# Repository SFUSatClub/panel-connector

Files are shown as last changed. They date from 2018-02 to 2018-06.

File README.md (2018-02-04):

# panel-connector
KiCad project of the connector board connecting the 4 outer panels to the internal PC104 stackup.

This repository uses the SFU Satellite Team's KiCad component library as a submodule.
To start working on the repository:

```
1. Open the git shell
2. Navigate to the directory you wish to place the repository inside
3. git clone --recursive "https://github.com/SFUSatClub/panel-connector.git"
4. cd .\panel-connector\KiCad-Lib\
5. git checkout master
```

If you modify either the component schematic or footprint libraries you must push those changes to the SFUSatClub/KiCad-Lib repository.

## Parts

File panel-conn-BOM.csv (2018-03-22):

reference | name | Digikey PN | number
R224,R3,R201,R211,R221,R231,R101,R111,R121 R223,R232,R233,R212,R215,R204,R205,R4,R131,R2*1,R1*1 | 0R | 311-0.0LBCT-ND | 21
J7 | B3B-XH-A(LF)(SN) | 455-2248-ND | 1
J7 | B3B-XH-A(LF)(SN) mating | 455-2219-ND | 1
J105,J2*0 | MOLEX_FFC-14 | WM1442CT-ND | 6
U2*0 | ADG728 | ADG728BRUZ-ND | 4
U1*0 | SPV1040 | 497-11417-ND | 8
L1*0 | L_10u0_10%_1.42A_2-SMD, | 495-5656-1-ND | 8
R1*5 | 1M0 | RG20P1.0MBCT-ND | 8
D1*0 | SMM4F5.0A-TR | 497-15660-1-ND | 8
C1*5 | 4u7F | 587-1302-1-ND | 8
C1*4,C1*0 | 10uF | 445-7658-1-ND | 16
R1*4 | 10m0 | WSLP-.01CT-ND | 8
R1*2, R1*3, R1*0 | 1k0 | RG20P1.0KBCT-ND | 24
C1*3, C1*2 | 1u0F | 445-1358-1-ND | 16
C1*1 | 100nF | 445-14401-1-ND | 8
R1*6 | 357k | P357KDACT-ND | 8

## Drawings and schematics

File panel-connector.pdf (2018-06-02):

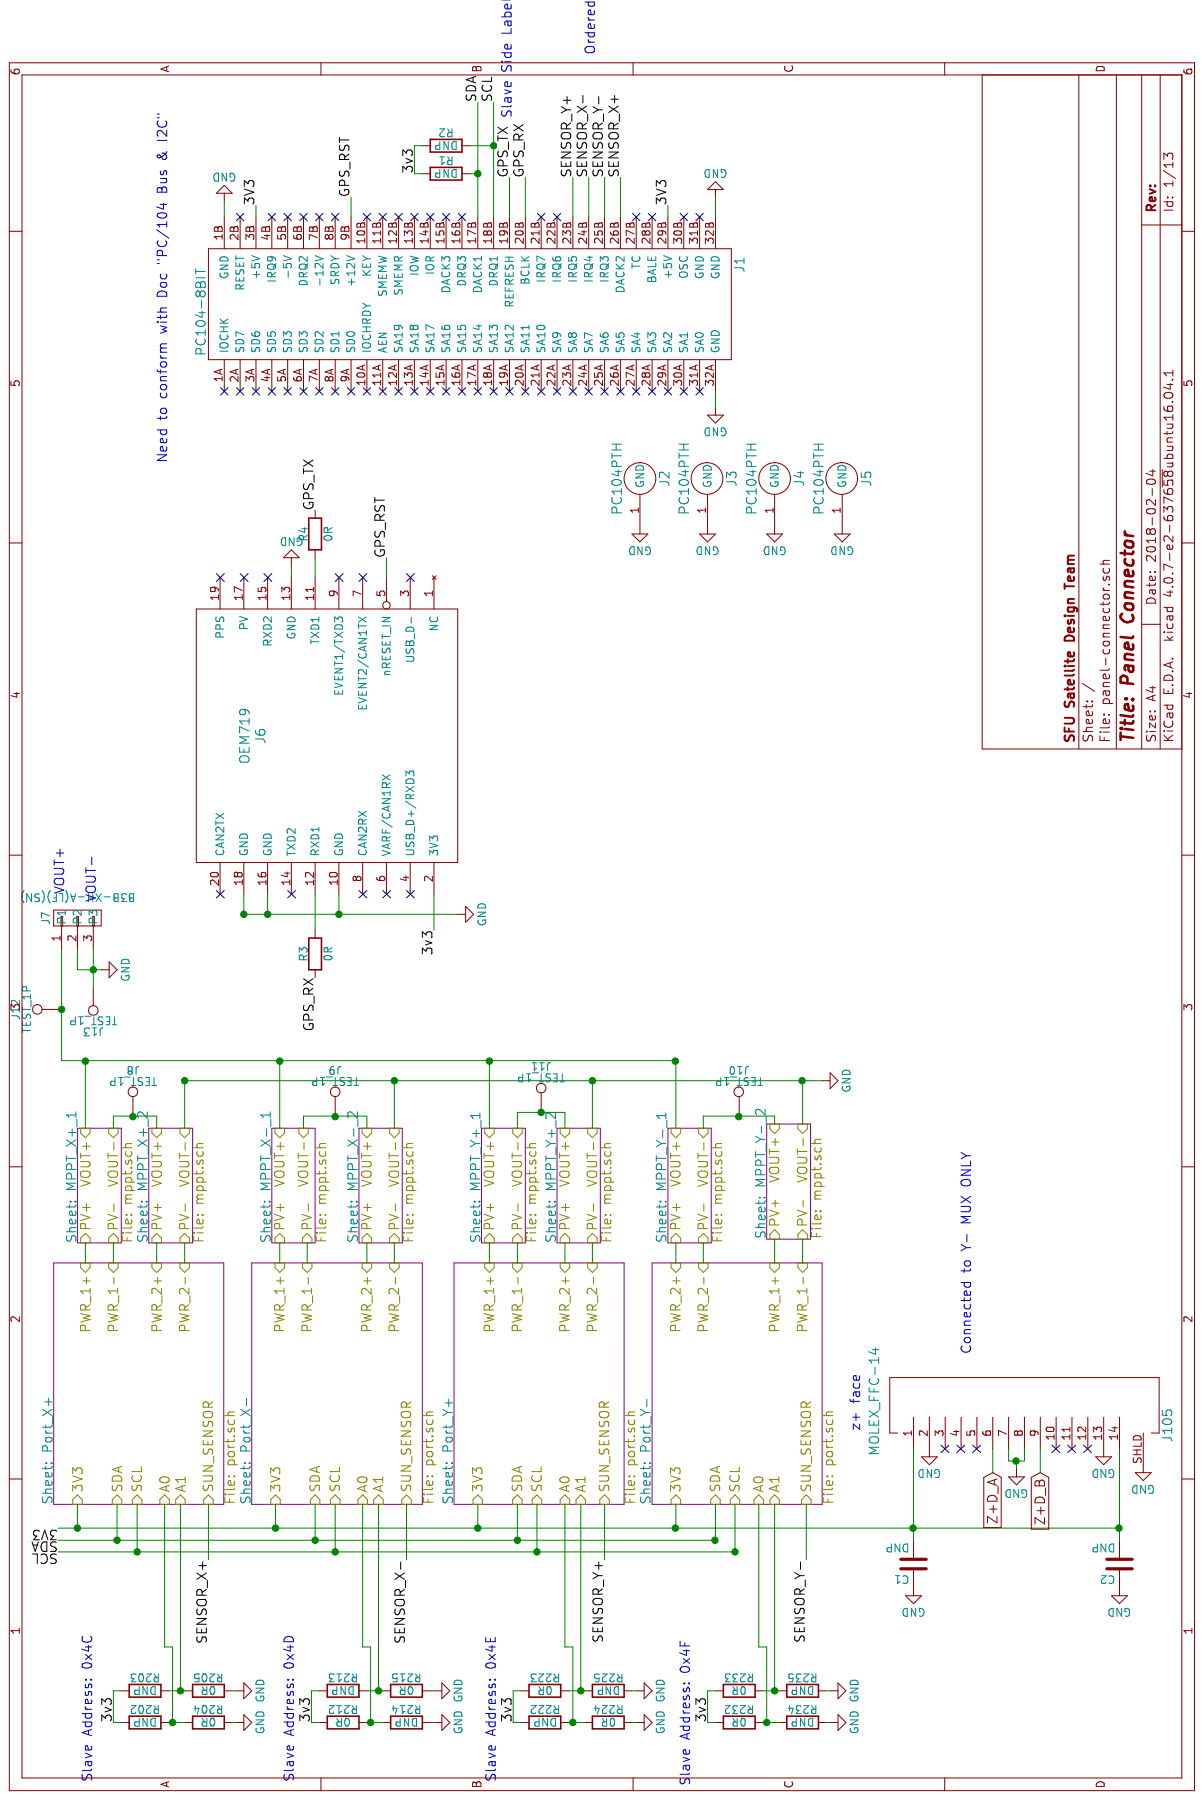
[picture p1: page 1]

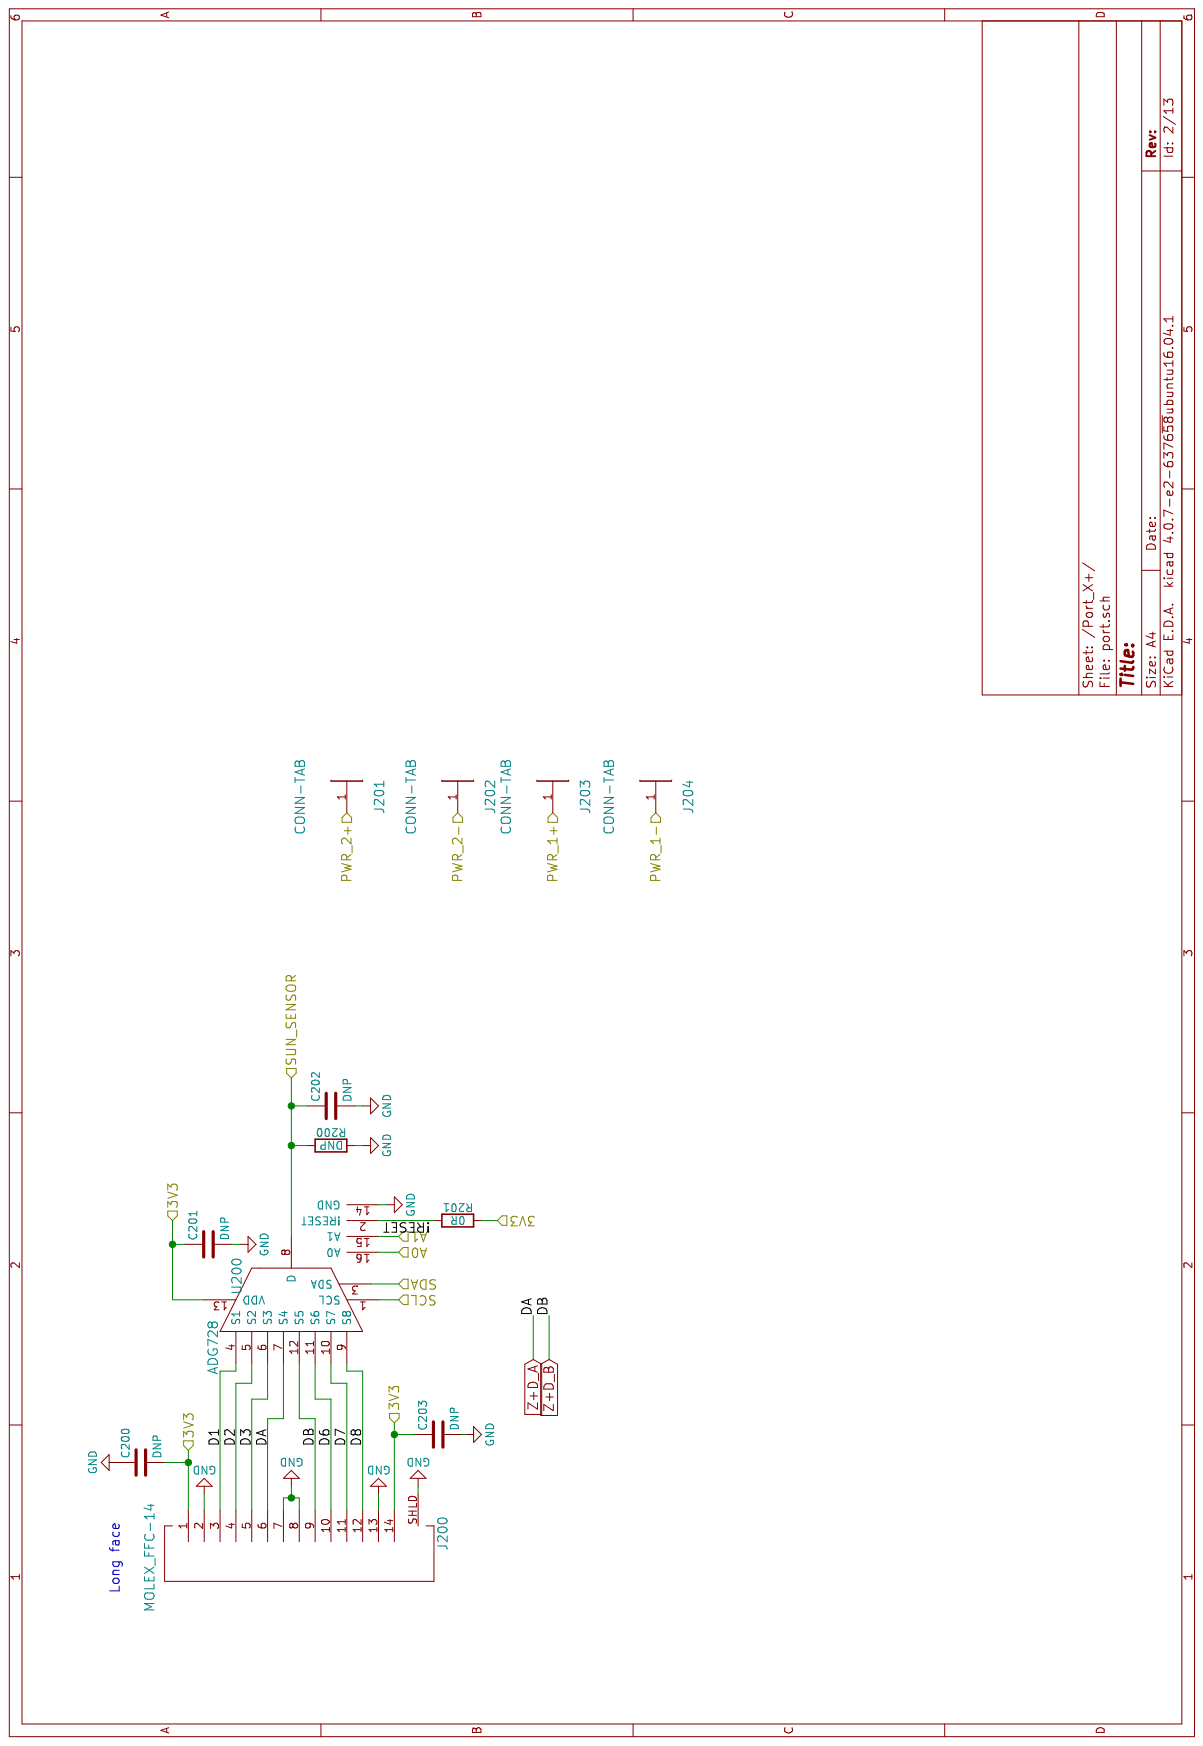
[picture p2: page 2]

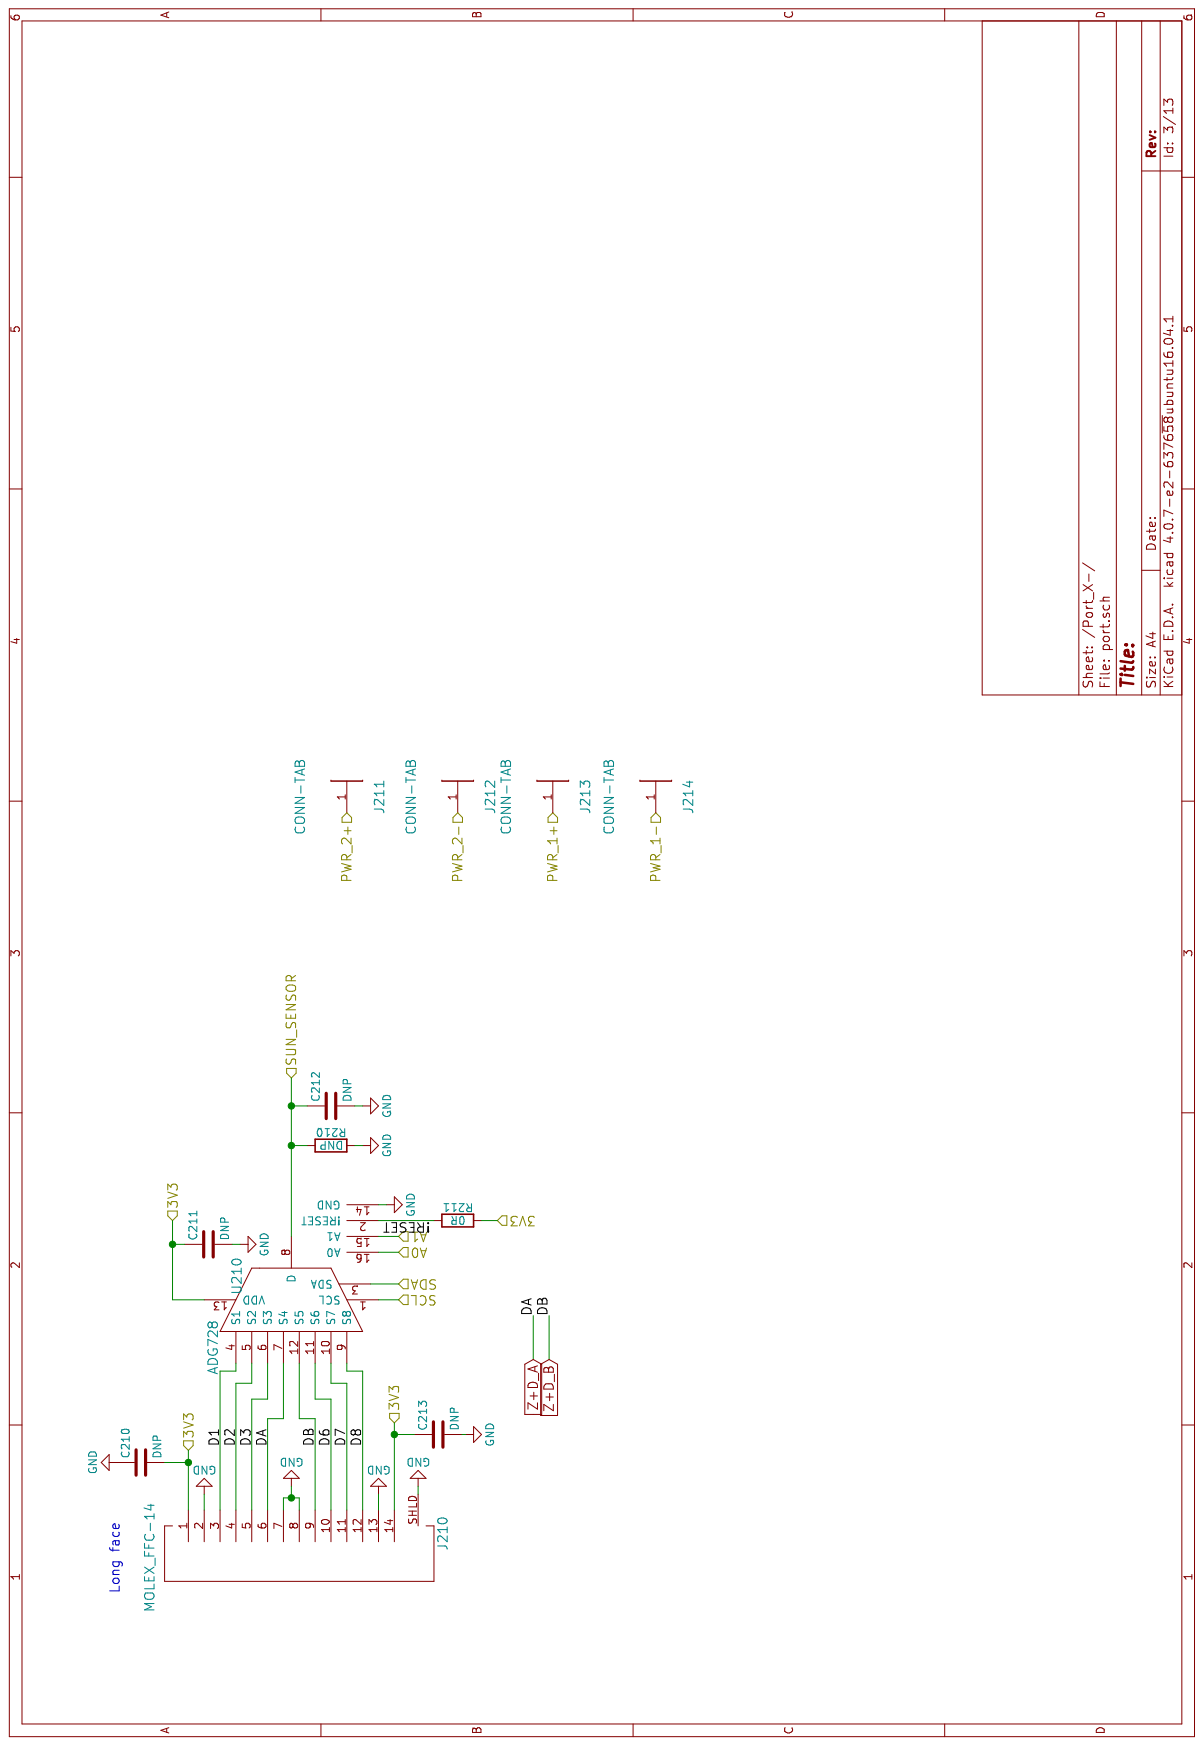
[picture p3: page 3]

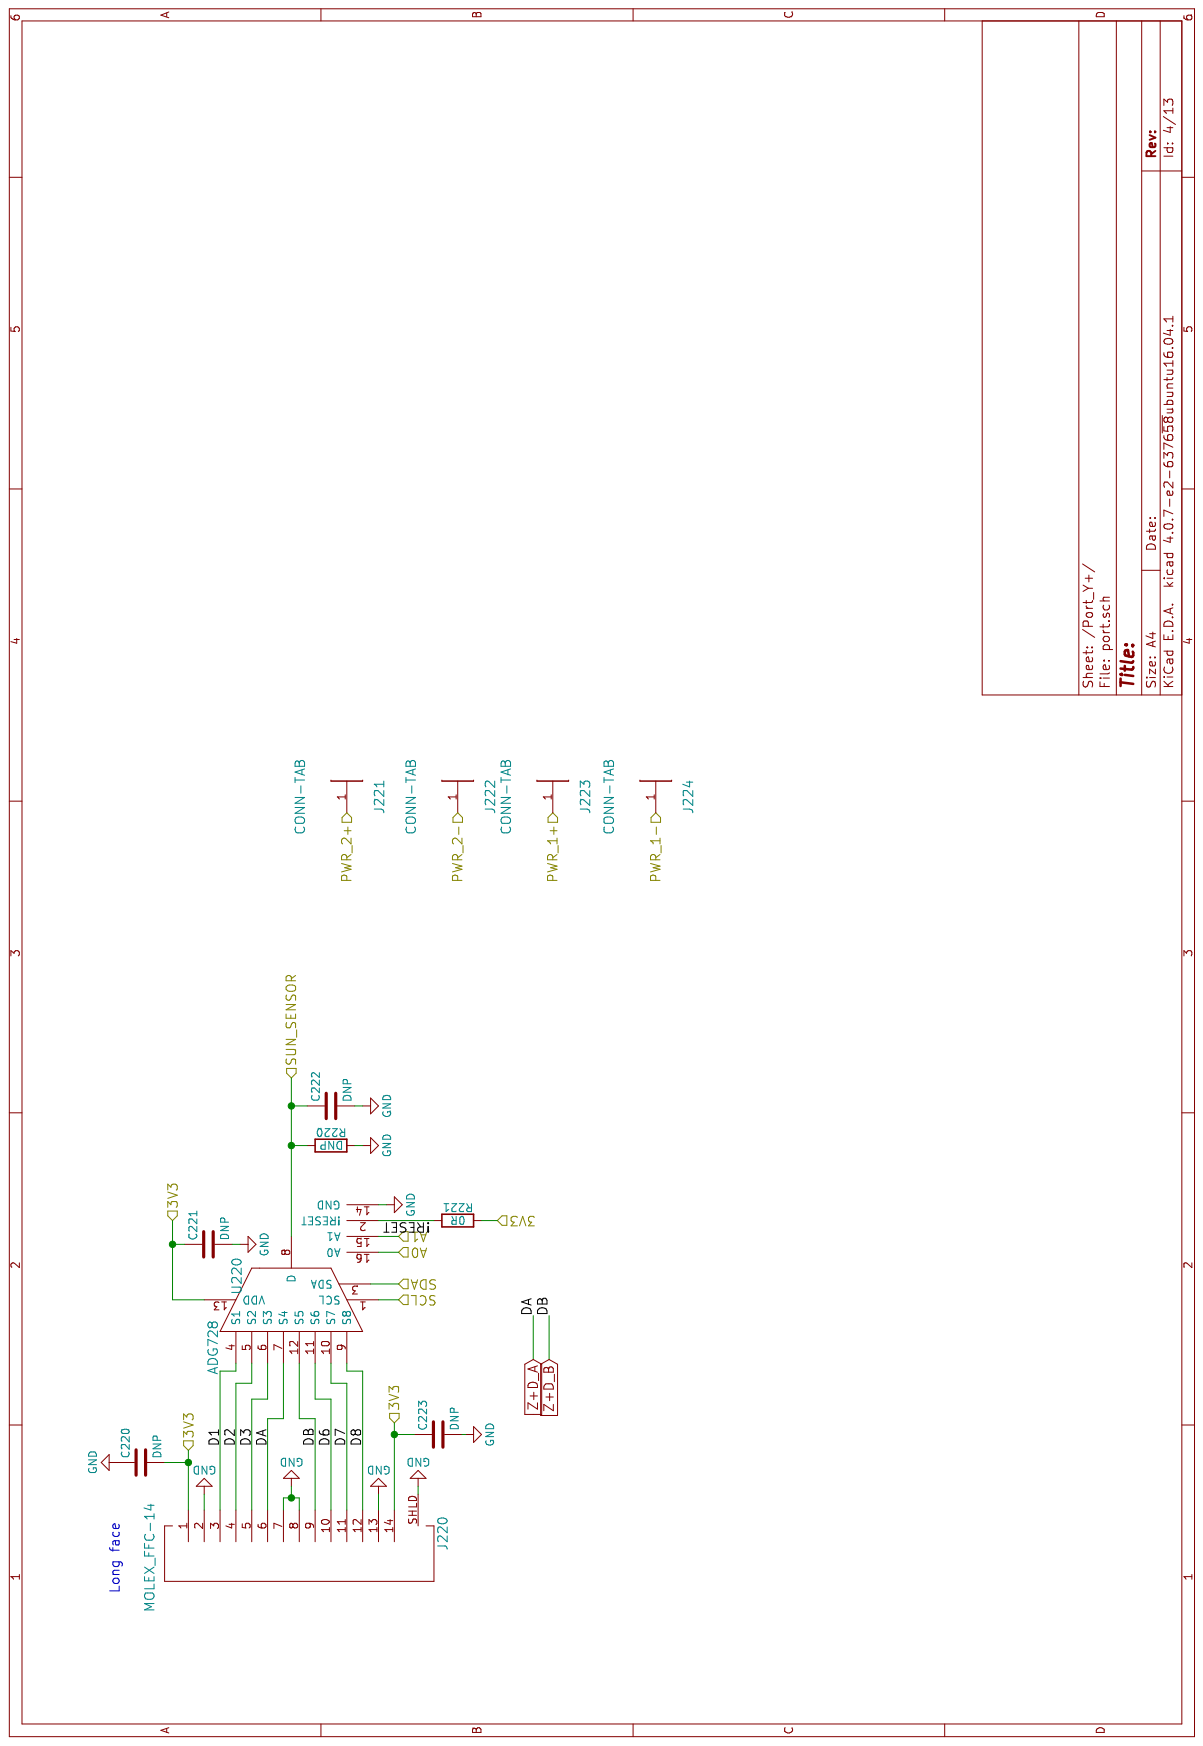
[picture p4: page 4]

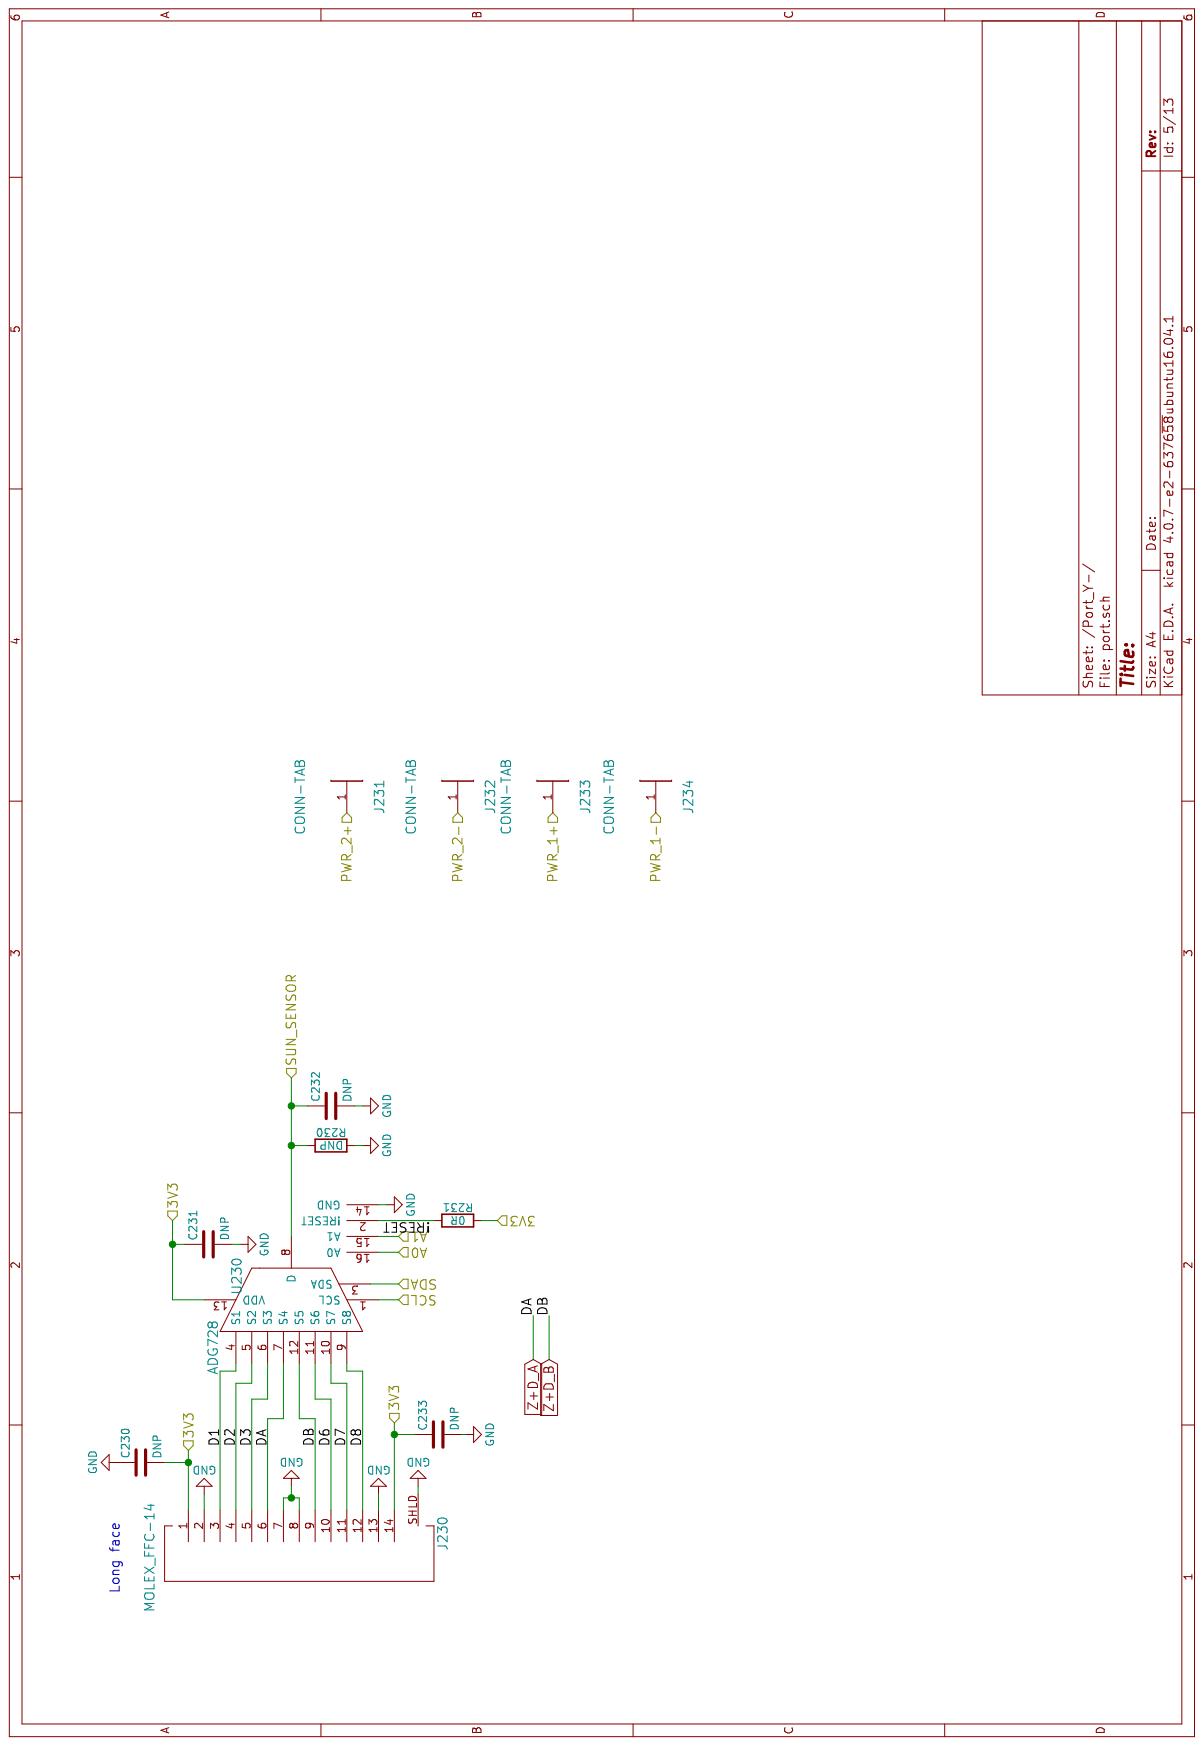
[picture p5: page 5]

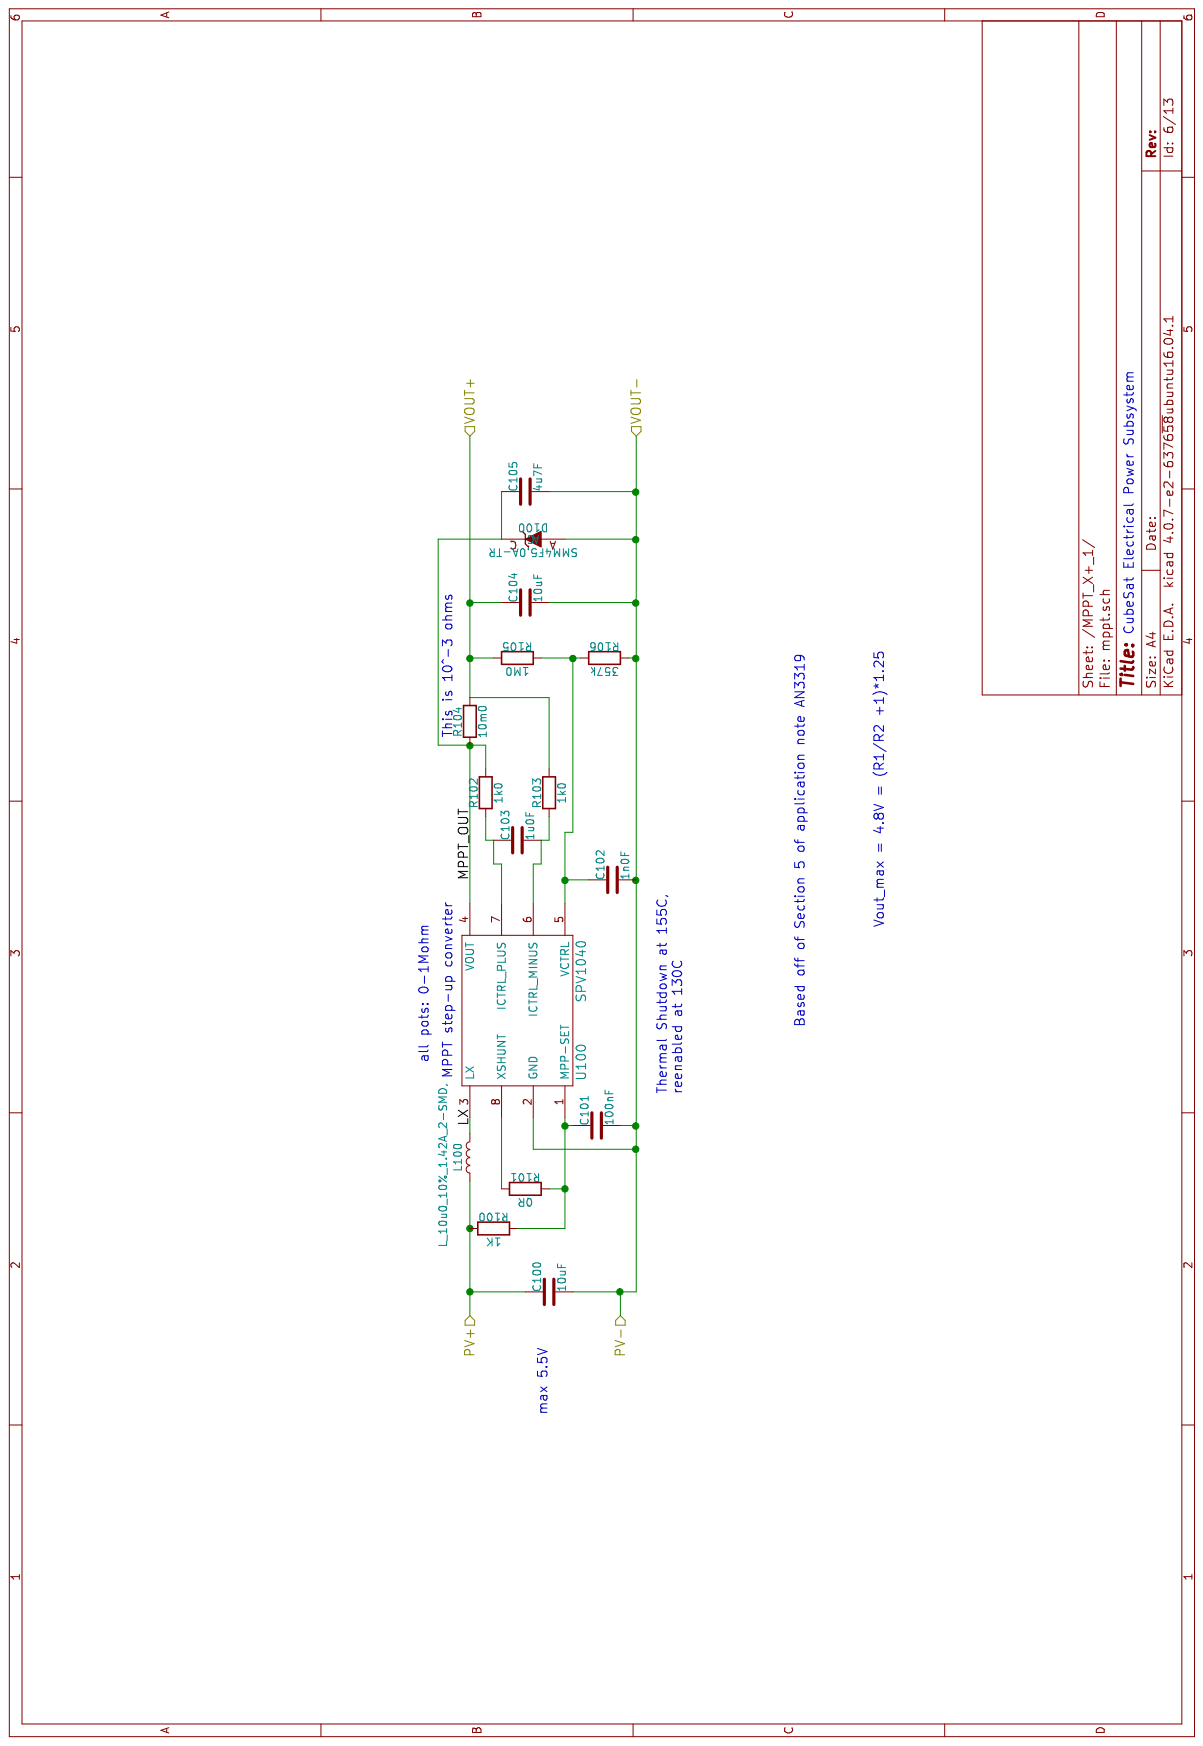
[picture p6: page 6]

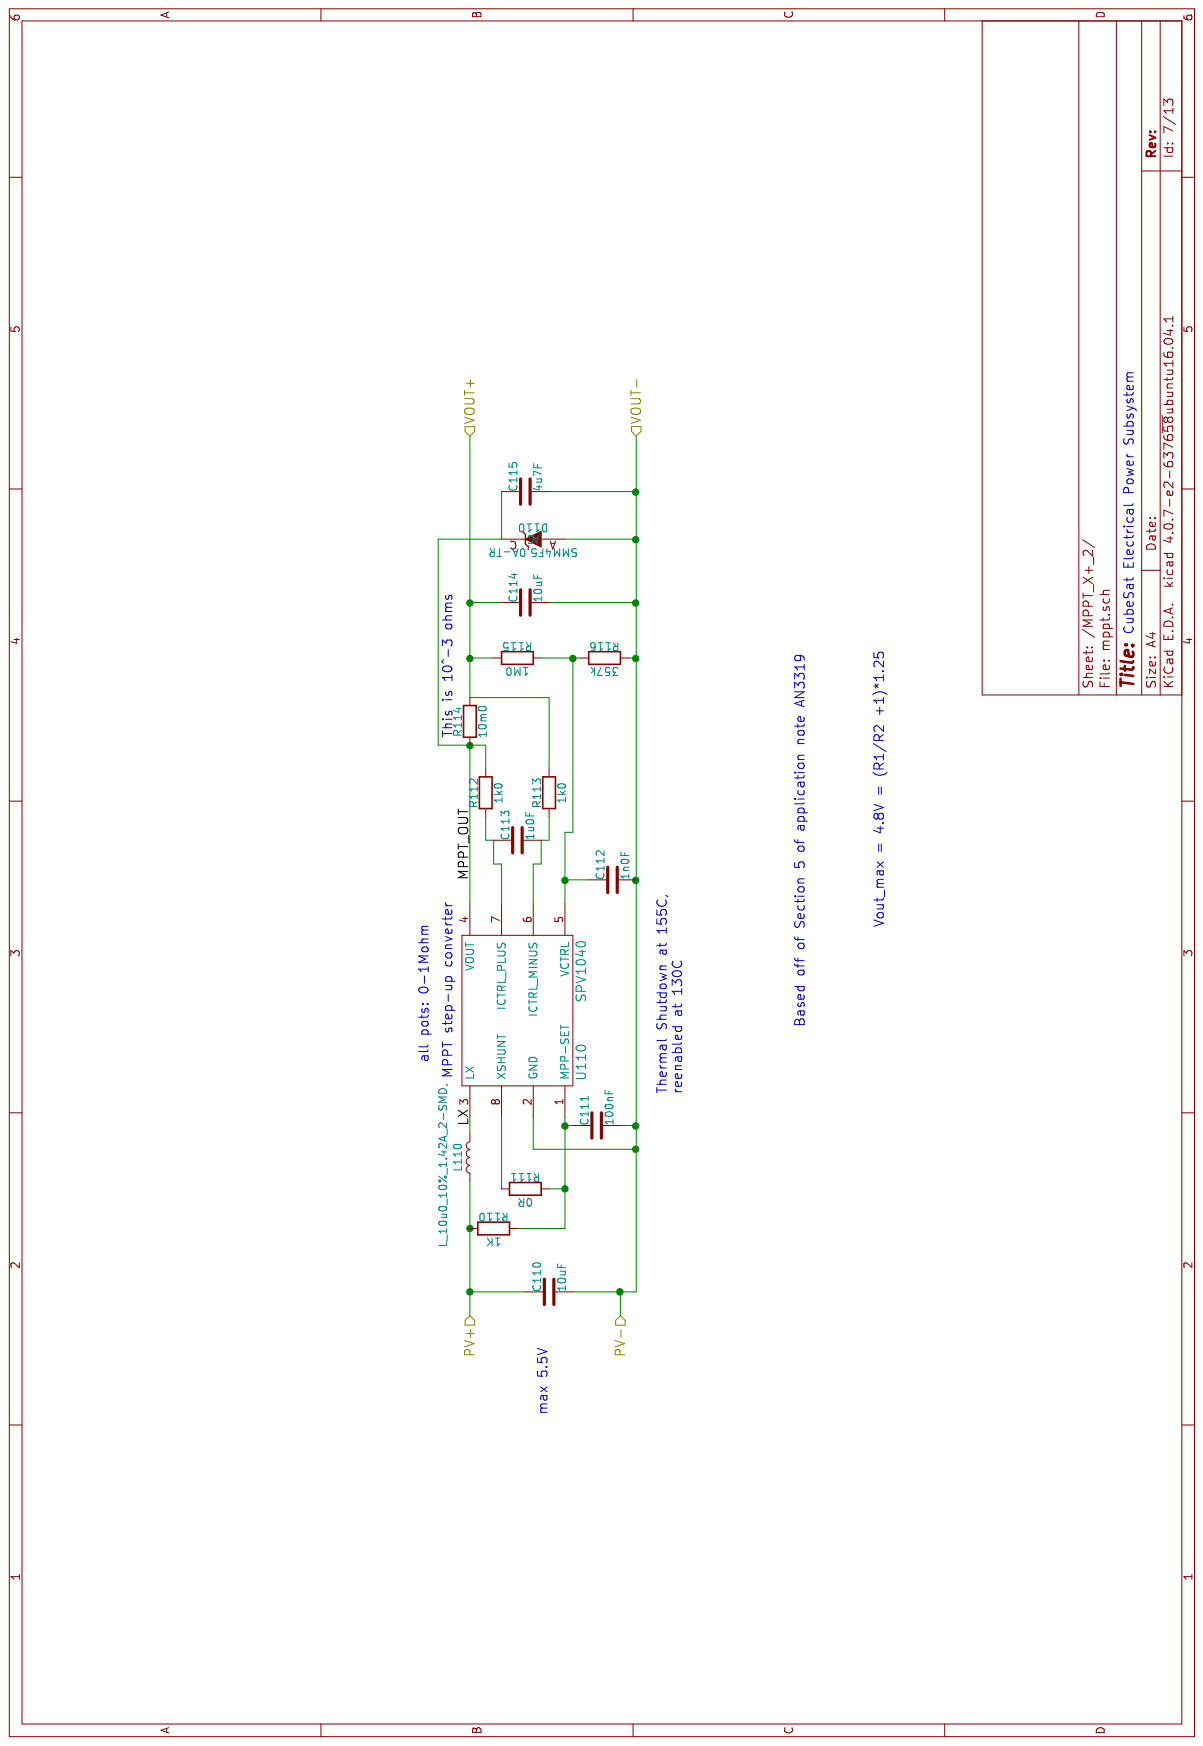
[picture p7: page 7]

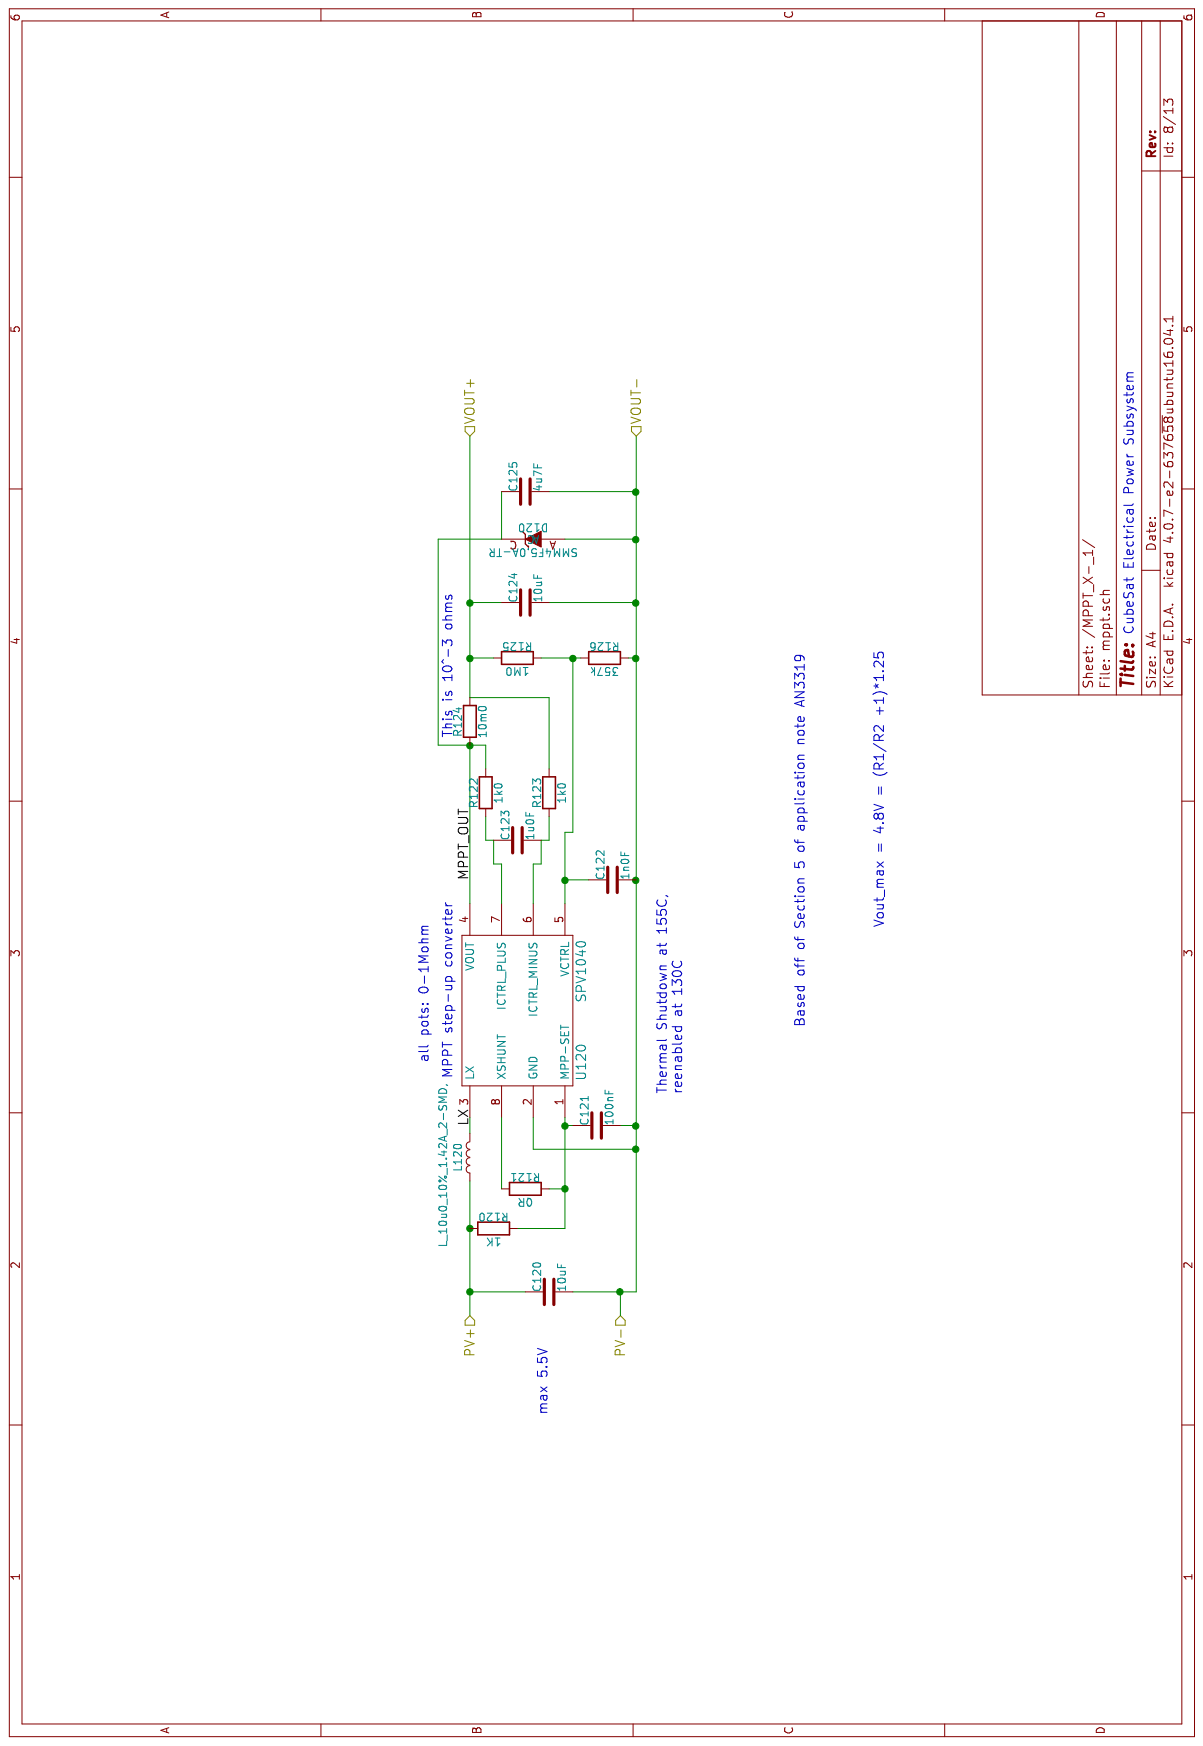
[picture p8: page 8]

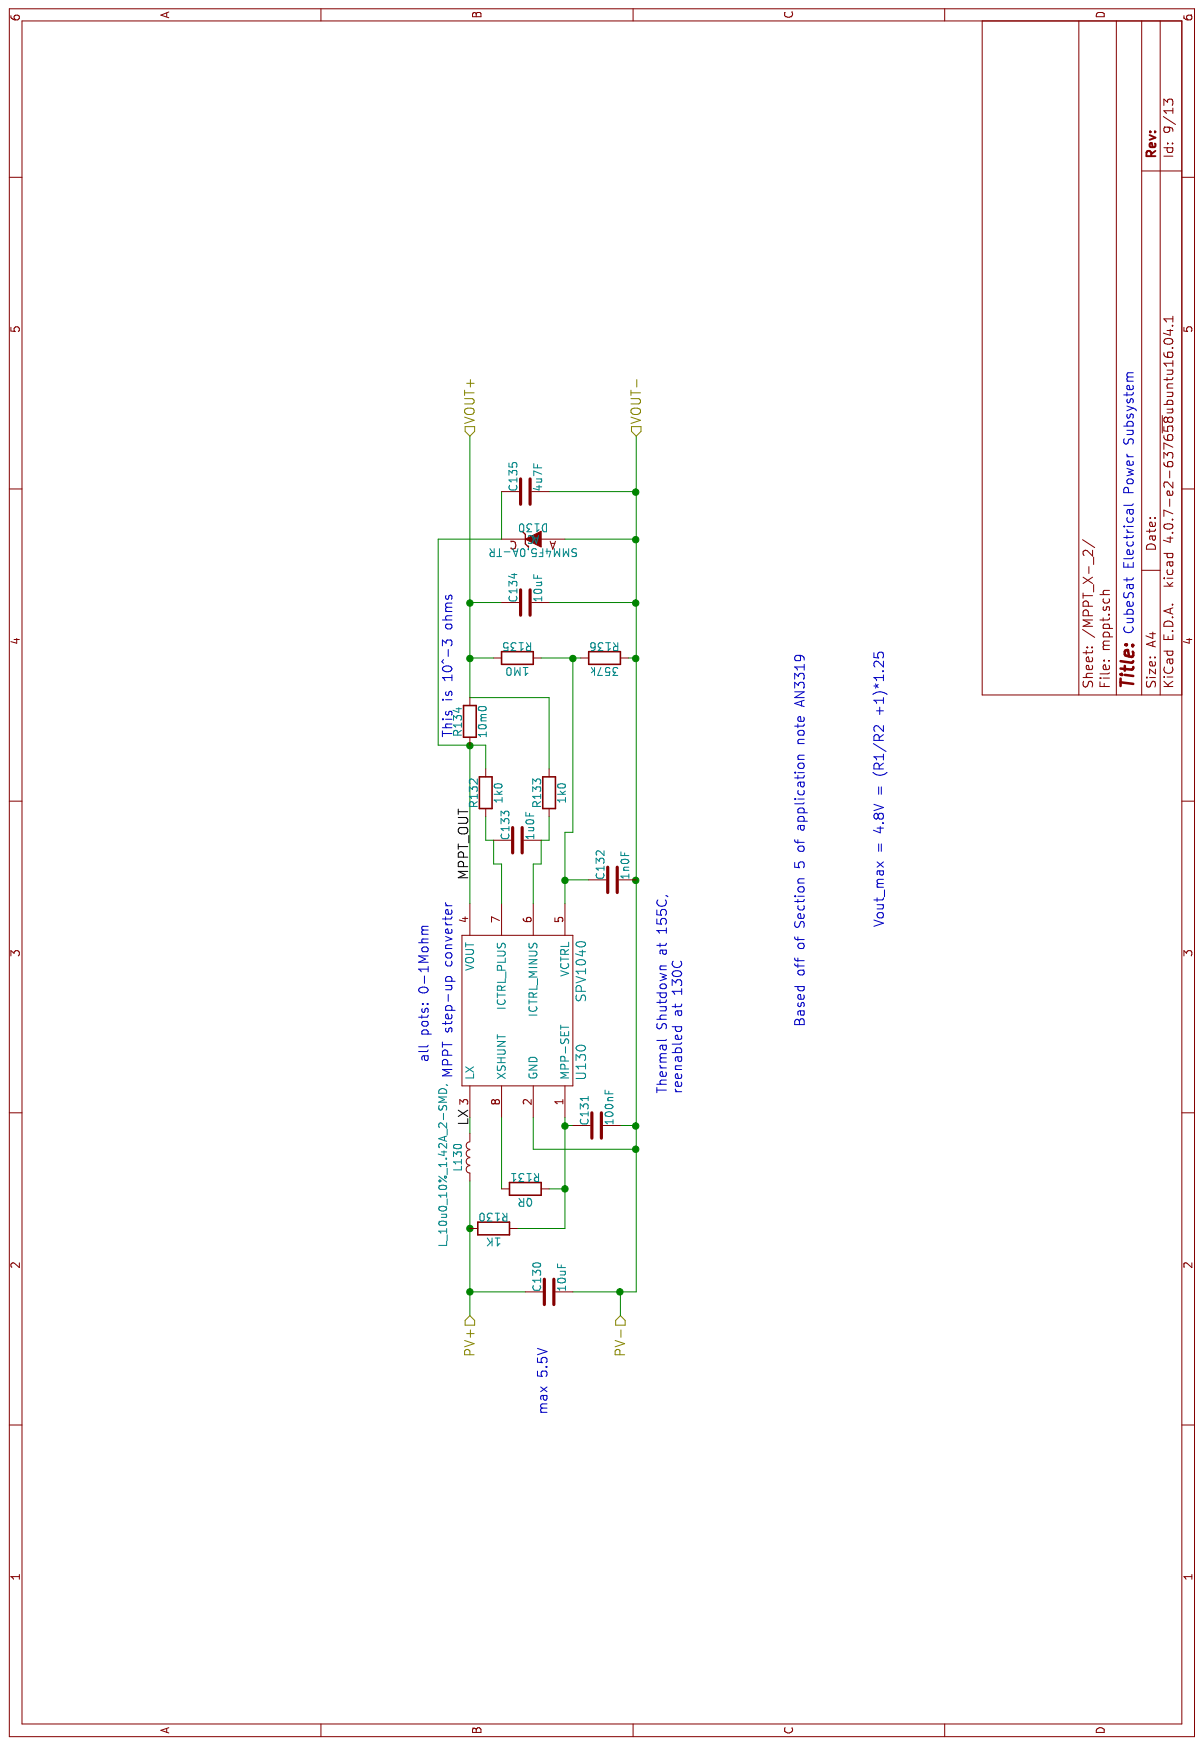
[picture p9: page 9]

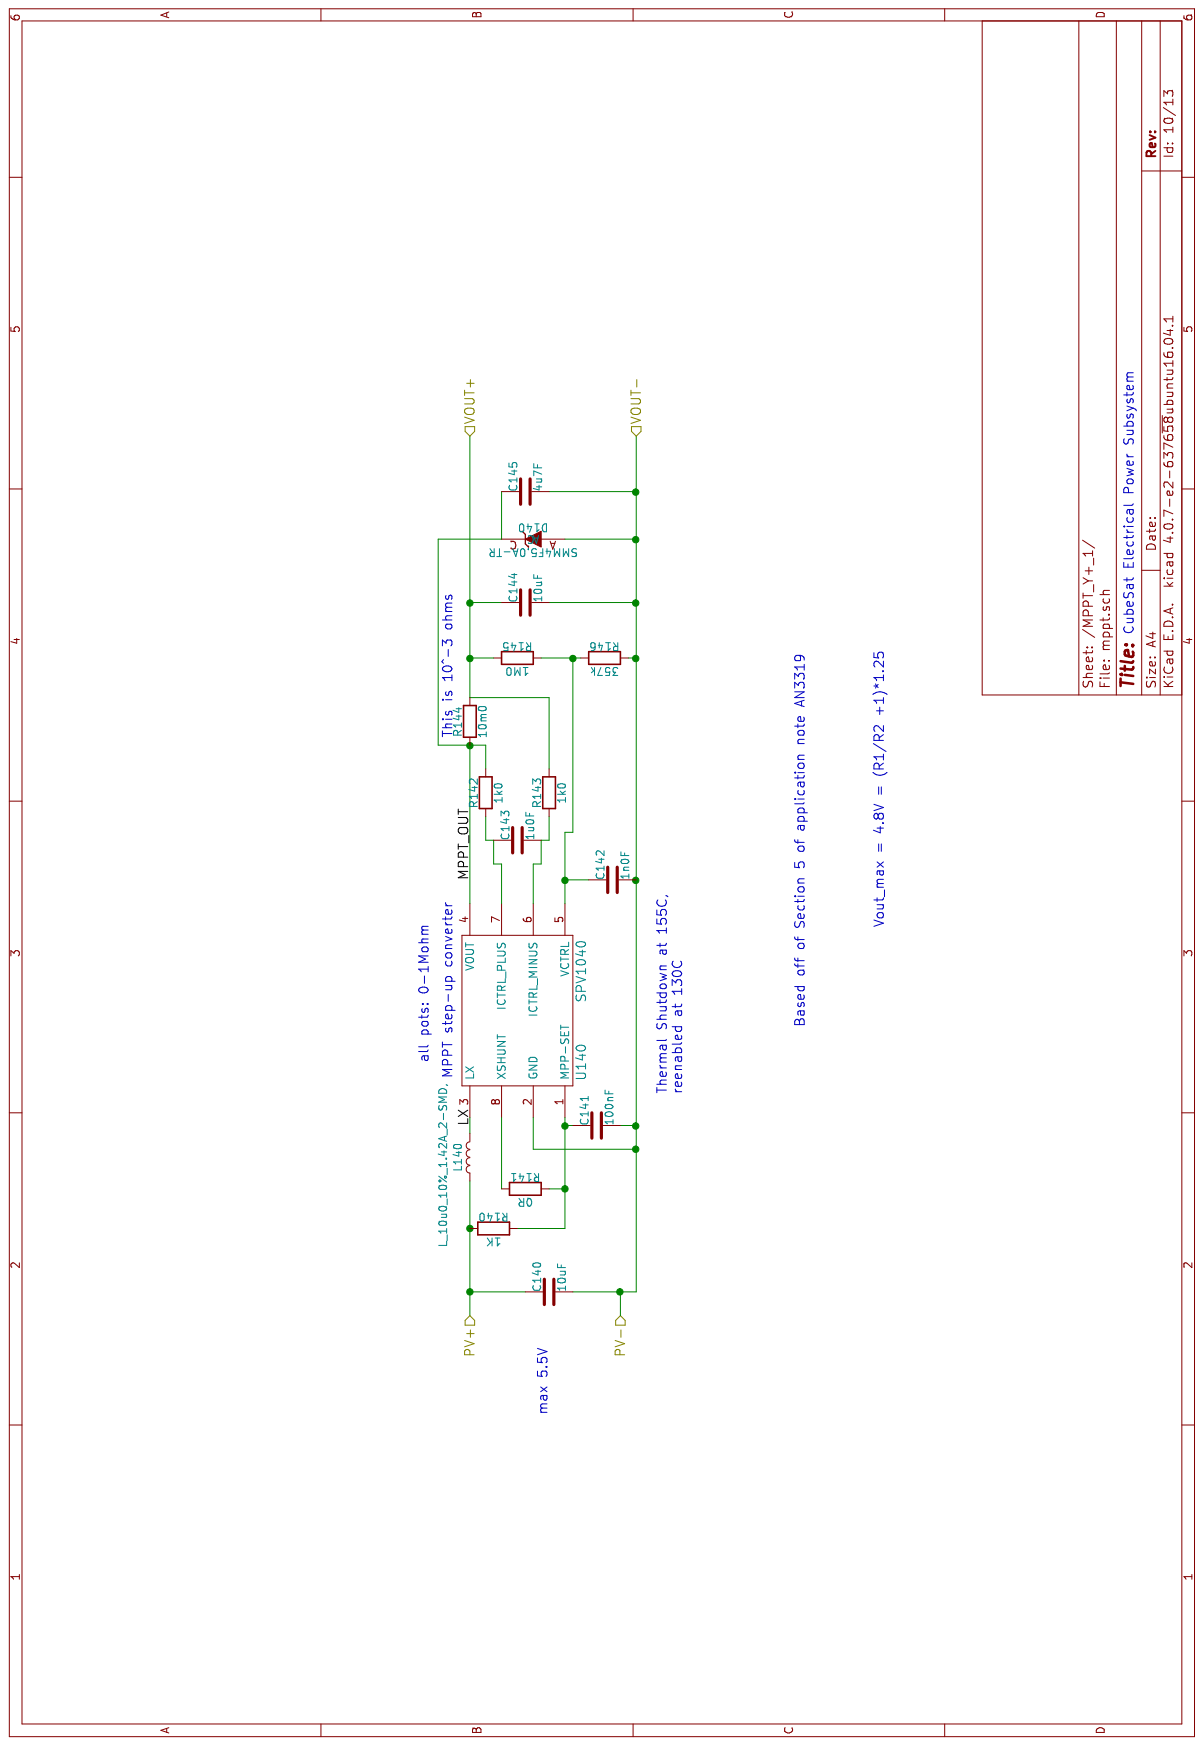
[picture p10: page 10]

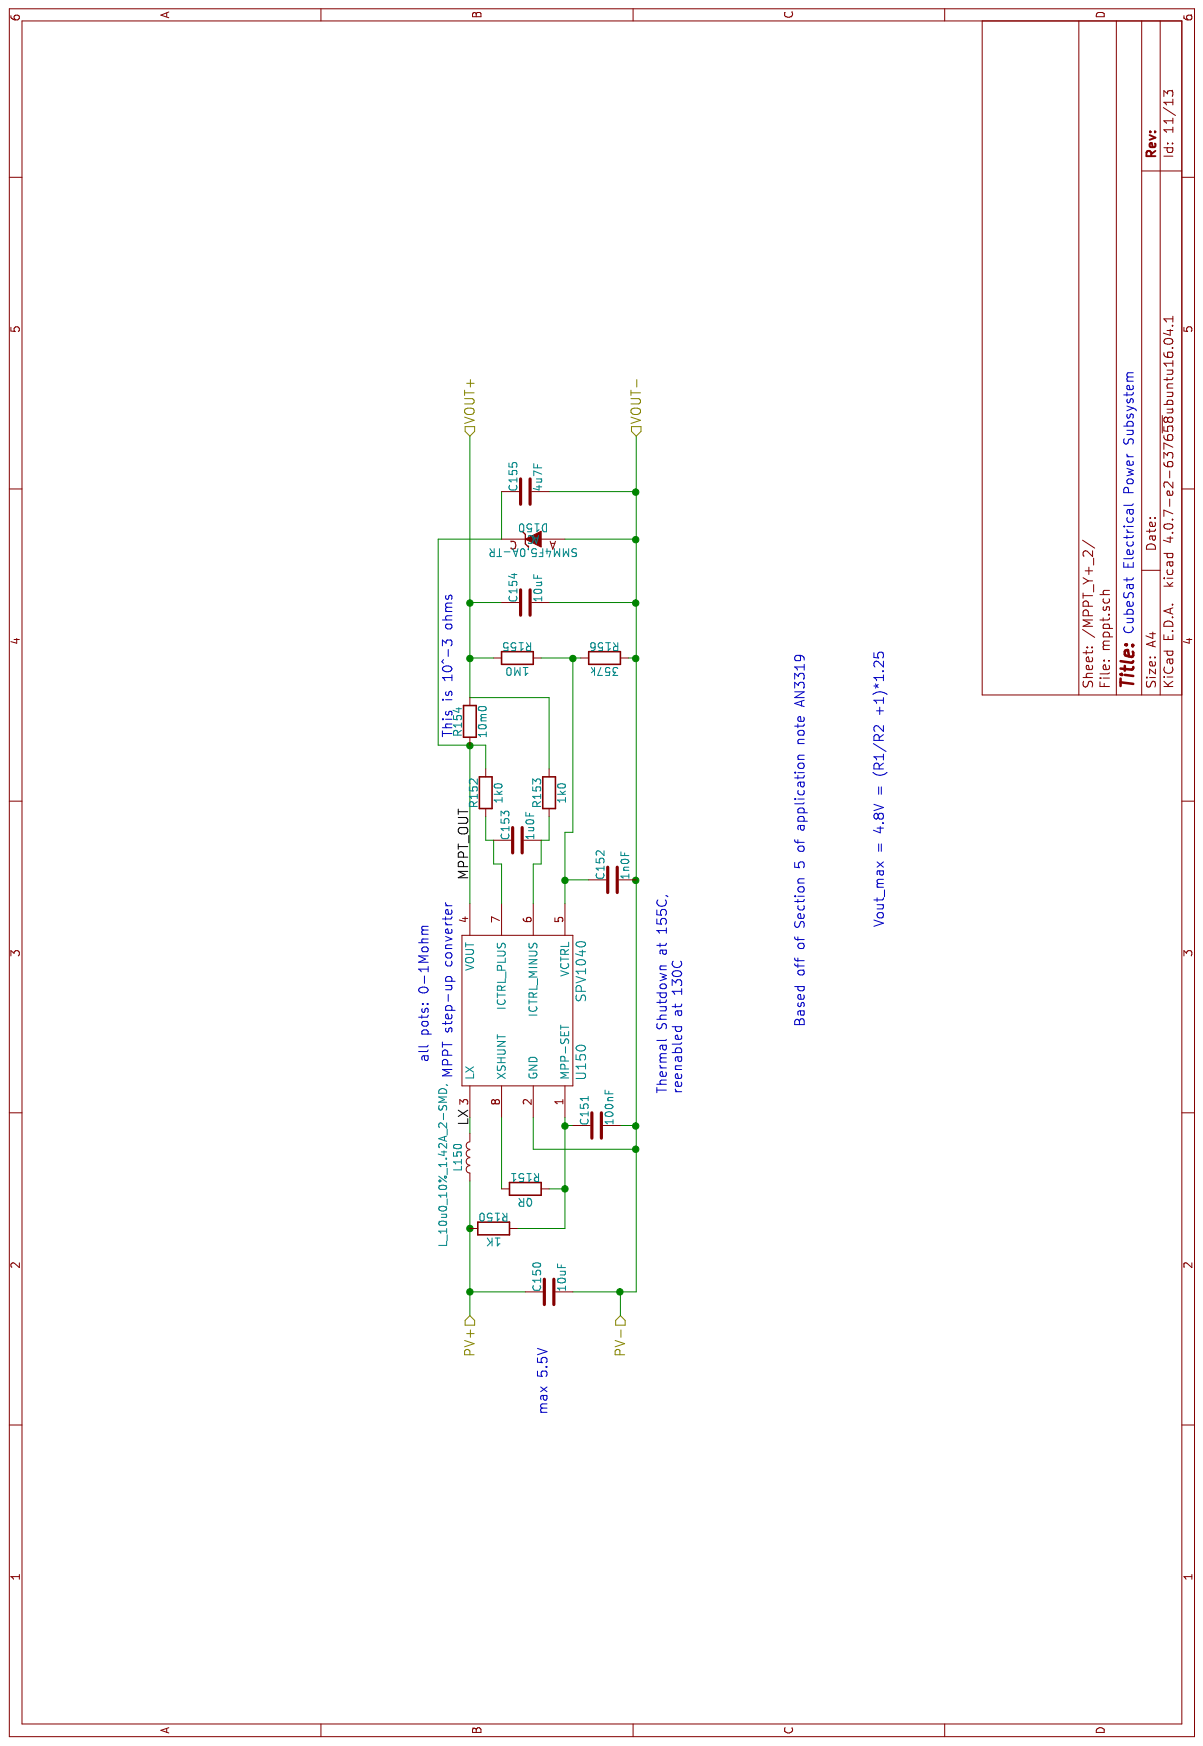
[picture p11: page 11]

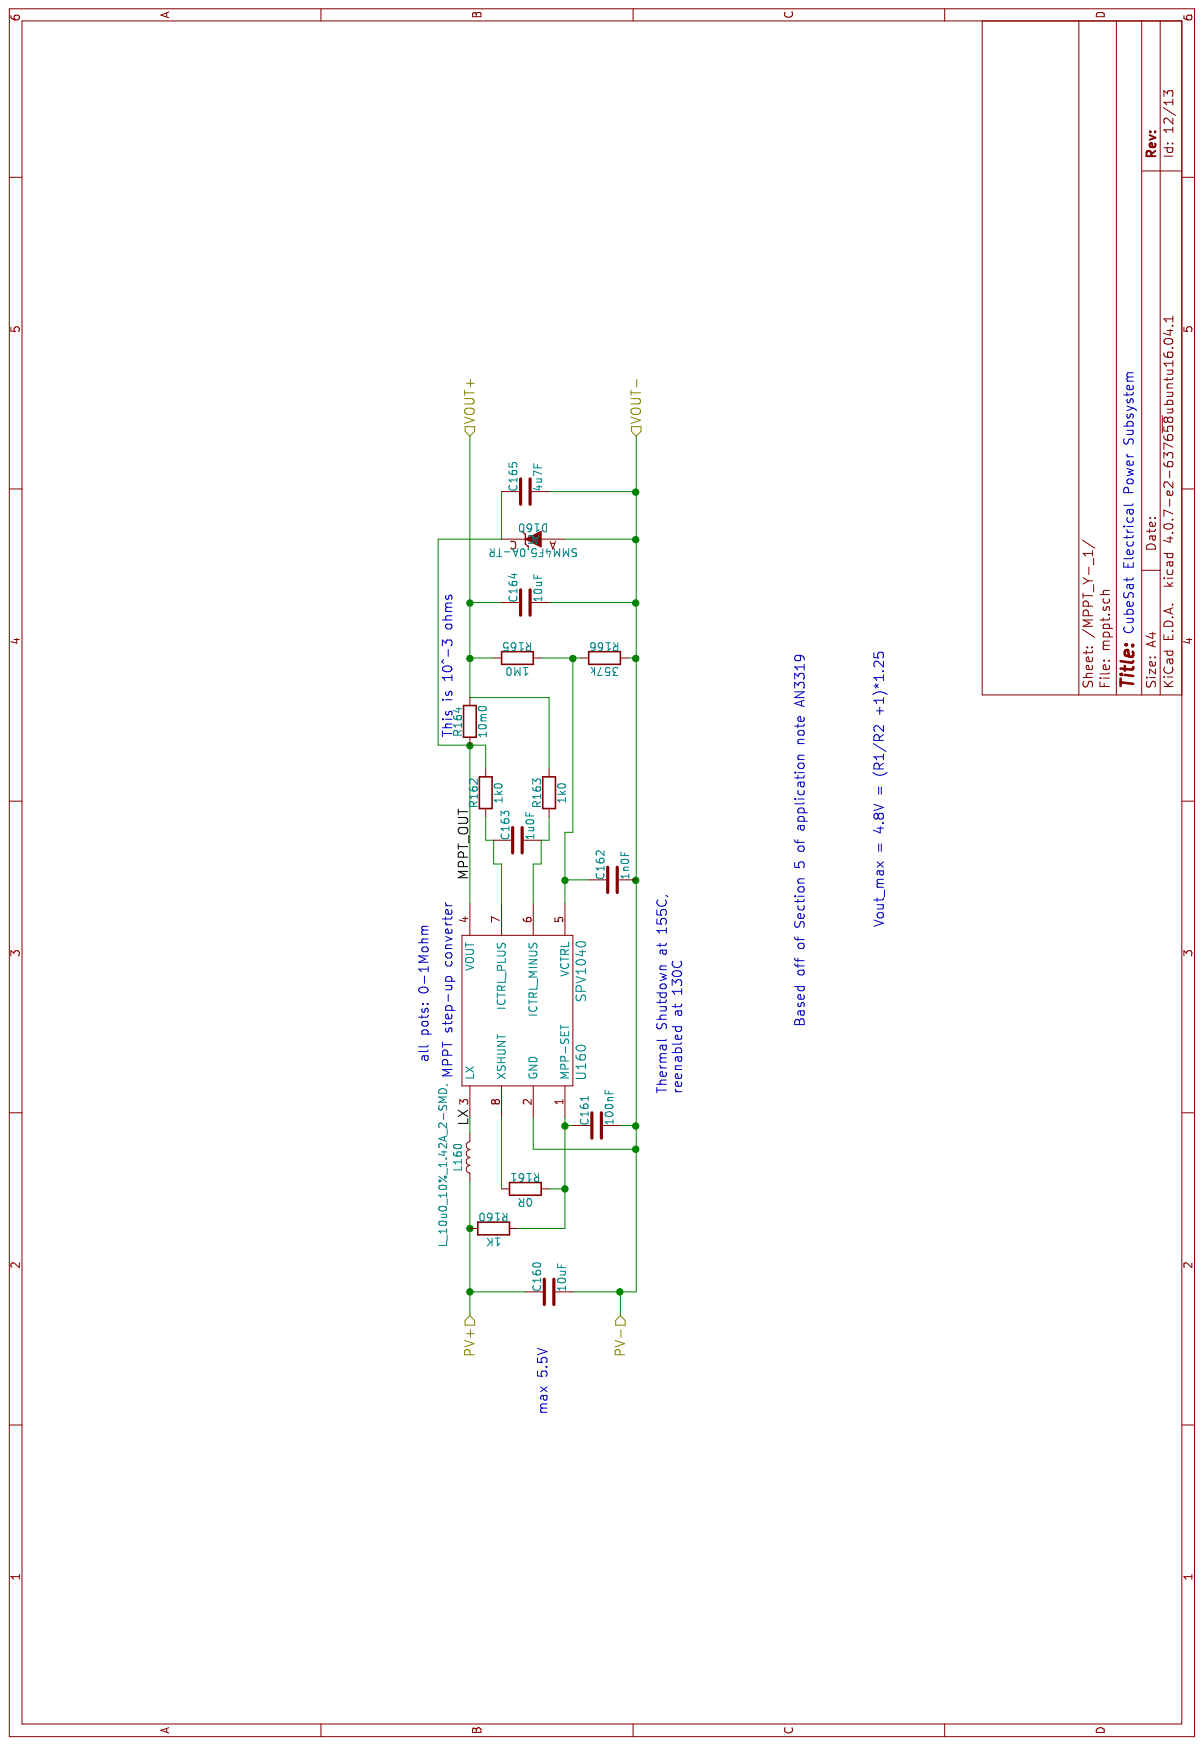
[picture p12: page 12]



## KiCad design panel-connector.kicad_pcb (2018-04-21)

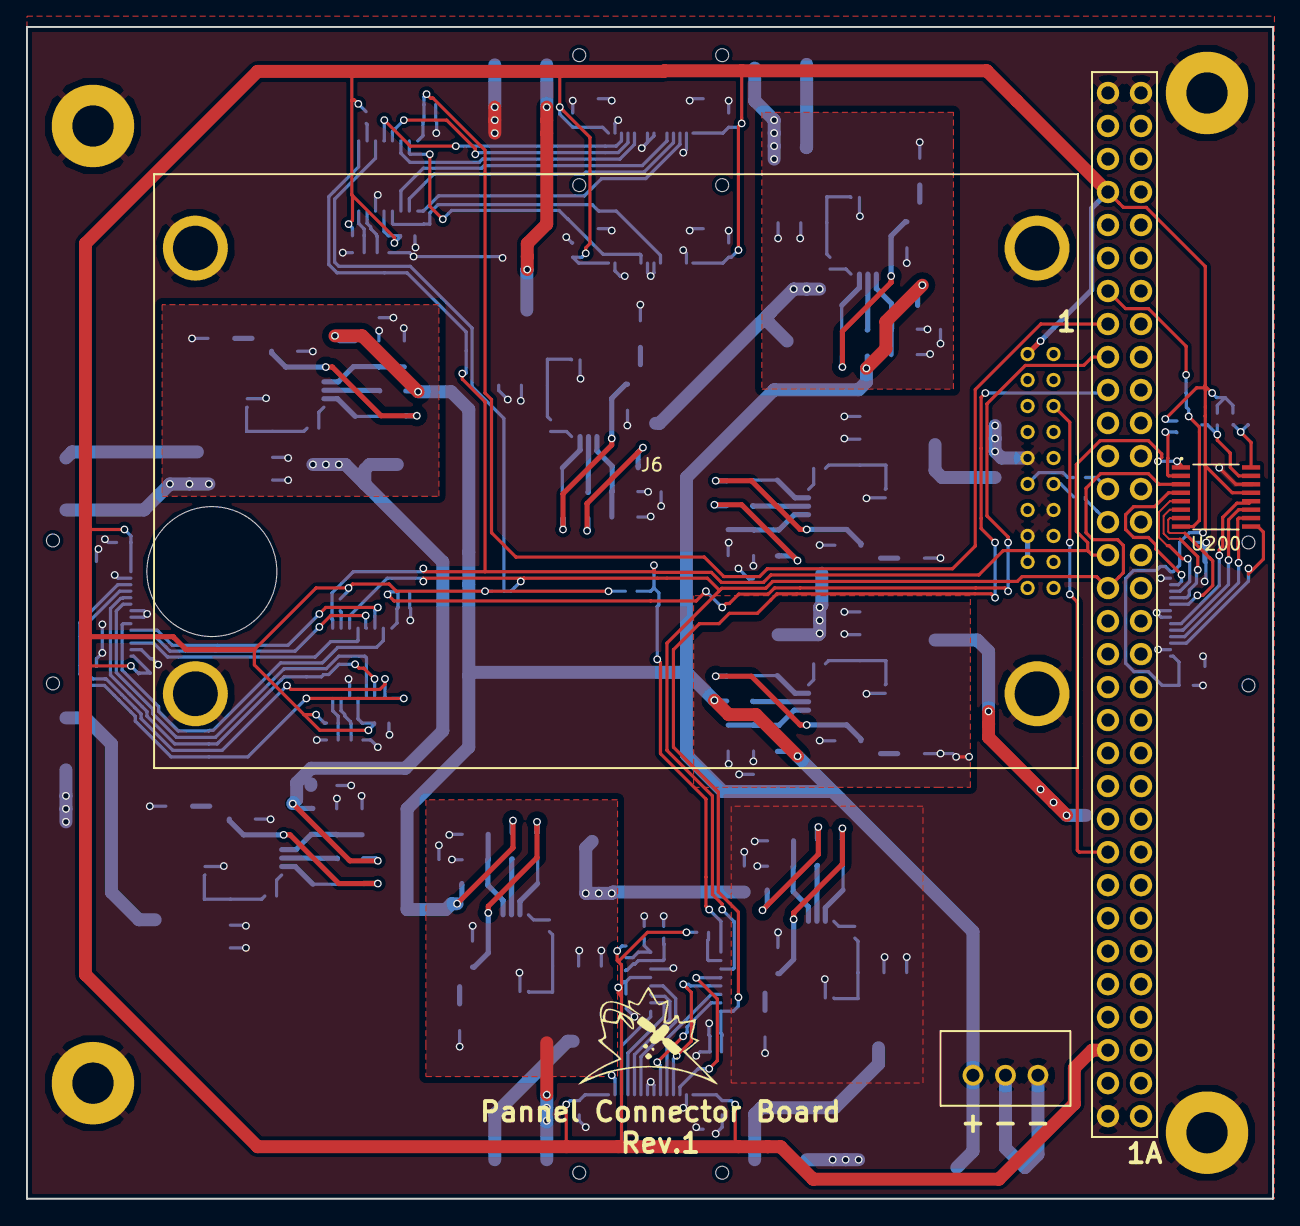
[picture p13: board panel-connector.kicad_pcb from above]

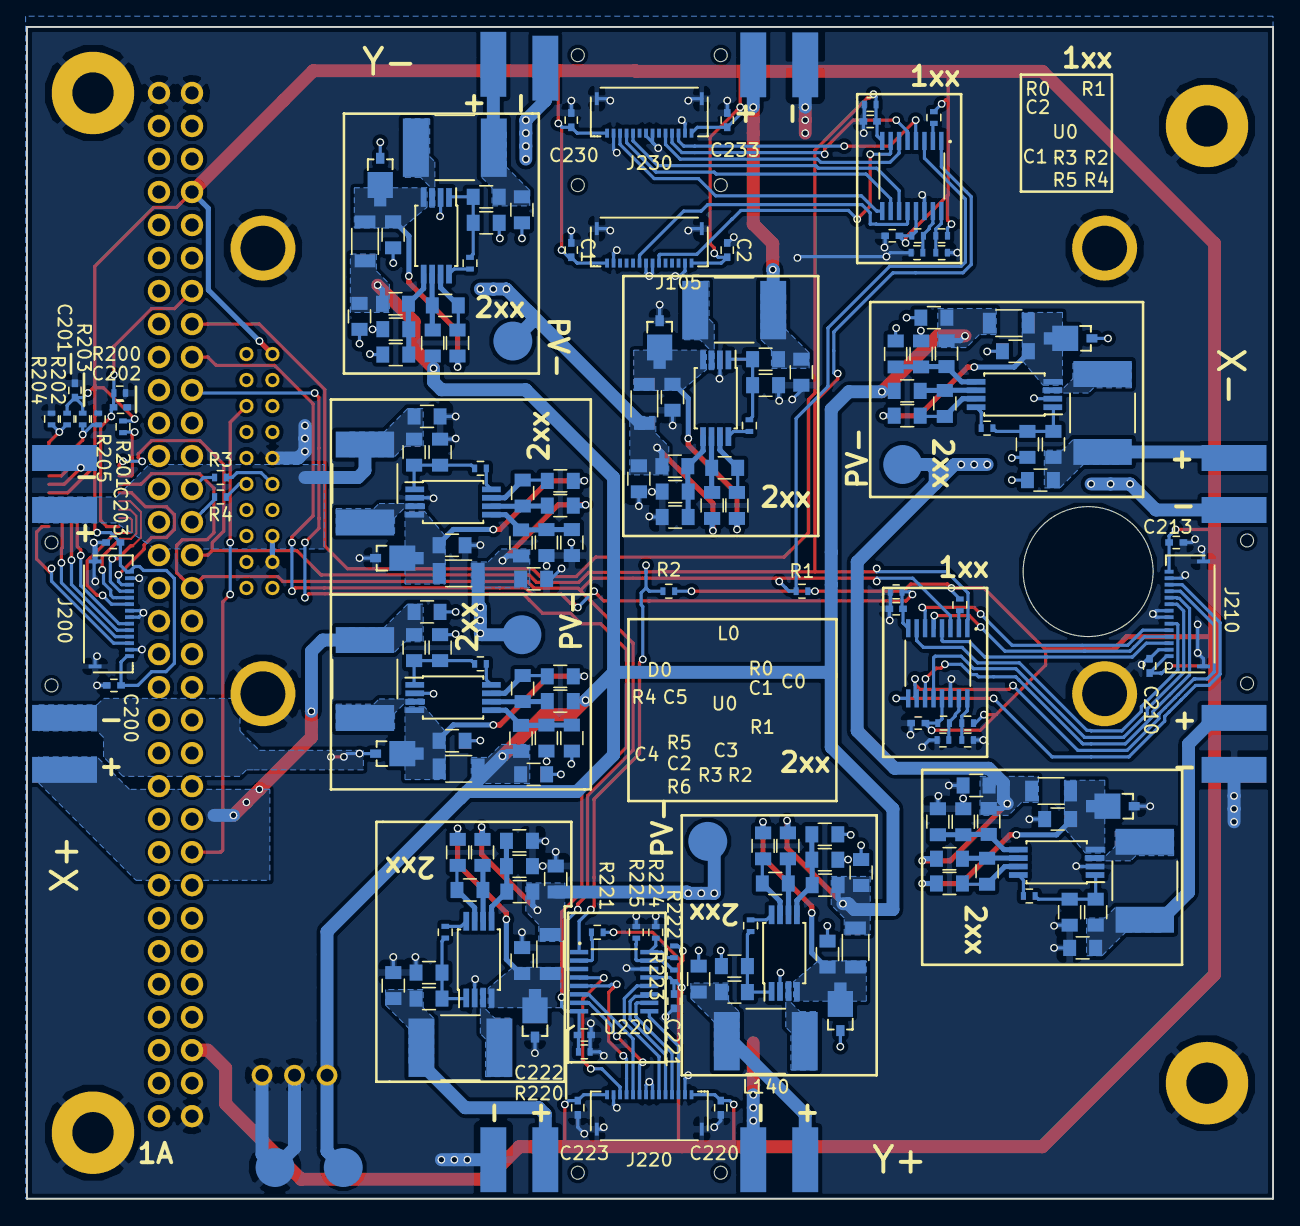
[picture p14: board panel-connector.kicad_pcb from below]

Board: 2 copper layers, 95.9 x 90.2 mm, 212 parts (204 on the bottom side), 120 nets.

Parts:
C1, C2, C200, C201, C202, C203, C210, C211, C212, C213, C220, C221, C222, C223, C230, C231, C232, C233: DNP; C_0402
C100, C104, C110, C114, C120, C124, C130, C134, C140, C144, C150, C154, C160, C164, C170, C174: 10uF; C_0805
C101, C111, C121, C131, C141, C151, C161, C171: 100nF; C_0805
C102, C112, C122, C132, C142, C152, C162, C172: 1n0F; C_0805
C103, C113, C123, C133, C143, C153, C163, C173: 1u0F; C_0805
C105, C115, C125, C135, C145, C155, C165, C175: 4u7F; C_0805
D100, D110, D120, D130, D140, D150, D160, D170: SMM4F5.0A-TR; SMM4F
J1: PC104-8BIT; PC104-8bit
J2, J3, J4, J5: PC104PTH
J6: OEM719
J7: B3B-XH-A(LF)(SN); B3B-XH-A
J8, J9, J10, J11, J12, J13: TEST_1P; Measurement_Point_Round-SMD-Pad_Big
J105, J200, J210, J220, J230: MOLEX_FFC-14
J201, J202, J203, J204, J211, J212, J213, J214, J221, J222, J223, J224, J231, J232, J233, J234: CONN-TAB; CONN_TAB
L100, L110, L120, L130, L140, L150, L160, L170: L_10u0_10%_1.42A_2-SMD,; L_2220
R1, R2, R200, R202, R203, R210, R213, R214, R220, R222, R225, R230, R234, R235: DNP; R_0402
R3, R4, R101, R111, R121, R131, R141, R151, R161, R171, R201, R204, R205, R211, R212, R215, R221, R223, R224, R231, R232, R233: 0R; R_0402
R100, R110, R120, R130, R140, R150, R160, R170: 1K; R_0805
R102, R103, R112, R113, R122, R123, R132, R133, R142, R143, R152, R153, R162, R163, R172, R173: 1k0; R_0805
R104, R114, R124, R134, R144, R154, R164, R174: 10m0; R_1206
R105, R115, R125, R135, R145, R155, R165, R175: 1M0; R_0805
R106, R116, R126, R136, R146, R156, R166, R176: 357k; R_0805
U100, U110, U120, U130, U140, U150, U160, U170: SPV1040; TSSOP-8_4.4x3mm_Pitch0.65mm
U200, U210, U220, U230: ADG728; TSSOP-16

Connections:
/3V3: C1.2, C2.2, C200.2, C201.1, C203.1, C210.2, C211.1, C213.1, C220.2, C221.1, C223.1, C230.2, C231.1, C233.1, J1.3B, J1.29B, J6.2, J105.1, J105.14, J200.1, J200.14, J210.1, J210.14, J220.1, J220.14, J230.1, J230.14, R1.1, R2.1, R201.2, R202.1, R203.1, R211.2, R212.1, R213.1, R221.2, R222.1, R223.1, R231.2, R232.1, R233.1, U200.13, U210.13, U220.13, U230.13
/GPS_RST: J1.9B, J6.5
/GPS_RX: J1.20B, R3.1
/GPS_TX: J1.19B, R4.2
/MPPT_X+_1/LX: L100.2, U100.3
/MPPT_X+_1/MPPT_OUT: C105.1, D100.C, R102.1, R104.1, U100.4
/MPPT_X+_1/PV+: C100.1, J203.1, L100.1, R100.1
/MPPT_X+_1/PV-: C100.2, C101.2, C102.2, C104.2, C105.2, C114.1, D100.A, J8.1, J204.1, R106.2, R113.1, R114.2, R115.1, U100.2
/MPPT_X+_1/VOUT+: C104.1, C124.1, C144.1, C164.1, J7.1, J12.1, R103.1, R104.2, R105.1, R123.1, R124.2, R125.1, R143.1, R144.2, R145.1, R163.1, R164.2, R165.1
/MPPT_X+_2/LX: L110.2, U110.3
/MPPT_X+_2/MPPT_OUT: C115.1, D110.C, R112.1, R114.1, U110.4
/MPPT_X+_2/PV+: C110.1, J201.1, L110.1, R110.1
/MPPT_X-_1/LX: L120.2, U120.3
/MPPT_X-_1/MPPT_OUT: C125.1, D120.C, R122.1, R124.1, U120.4
/MPPT_X-_1/PV+: C120.1, J213.1, L120.1, R120.1
/MPPT_X-_1/PV-: C120.2, C121.2, C122.2, C124.2, C125.2, C134.1, D120.A, J9.1, J214.1, R126.2, R133.1, R134.2, R135.1, U120.2
/MPPT_X-_2/LX: L130.2, U130.3
/MPPT_X-_2/MPPT_OUT: C135.1, D130.C, R132.1, R134.1, U130.4
/MPPT_X-_2/PV+: C130.1, J211.1, L130.1, R130.1
/MPPT_Y+_1/LX: L140.2, U140.3
/MPPT_Y+_1/MPPT_OUT: C145.1, D140.C, R142.1, R144.1, U140.4
/MPPT_Y+_1/PV+: C140.1, J223.1, L140.1, R140.1
/MPPT_Y+_1/PV-: C140.2, C141.2, C142.2, C144.2, C145.2, C154.1, D140.A, J11.1, J224.1, R146.2, R153.1, R154.2, R155.1, U140.2
/MPPT_Y+_2/LX: L150.2, U150.3
/MPPT_Y+_2/MPPT_OUT: C155.1, D150.C, R152.1, R154.1, U150.4
/MPPT_Y+_2/PV+: C150.1, J221.1, L150.1, R150.1
/MPPT_Y-_1/LX: L160.2, U160.3
/MPPT_Y-_1/MPPT_OUT: C165.1, D160.C, R162.1, R164.1, U160.4
/MPPT_Y-_1/PV+: C160.1, J231.1, L160.1, R160.1
/MPPT_Y-_1/PV-: C160.2, C161.2, C162.2, C164.2, C165.2, C174.1, D160.A, J10.1, J232.1, R166.2, R173.1, R174.2, R175.1, U160.2
/MPPT_Y-_2/LX: L170.2, U170.3
/MPPT_Y-_2/MPPT_OUT: C175.1, D170.C, R172.1, R174.1, U170.4
/MPPT_Y-_2/PV+: C170.1, J233.1, L170.1, R170.1
/Port_X+/!RESET: R201.1, U200.2
/Port_X+/A0: R202.2, R204.1, U200.16
/Port_X+/A1: R203.2, R205.1, U200.15
/Port_X+/D1: J200.3, U200.4
/Port_X+/D2: J200.4, U200.5
/Port_X+/D3: J200.5, U200.6
/Port_X+/D6: J200.10, U200.11
/Port_X+/D7: J200.11, U200.10
/Port_X+/D8: J200.12, U200.9
/Port_X-/!RESET: R211.1, U210.2
/Port_X-/A0: R212.2, R214.1, U210.16
/Port_X-/A1: R213.2, R215.1, U210.15
/Port_X-/D1: J210.3, U210.4
/Port_X-/D2: J210.4, U210.5
/Port_X-/D3: J210.5, U210.6
/Port_X-/D6: J210.10, U210.11
/Port_X-/D7: J210.11, U210.10
/Port_X-/D8: J210.12, U210.9
/Port_Y+/!RESET: R221.1, U220.2
/Port_Y+/A0: R222.2, R224.1, U220.16
/Port_Y+/A1: R223.2, R225.1, U220.15
/Port_Y+/D1: J220.3, U220.4
/Port_Y+/D2: J220.4, U220.5
/Port_Y+/D3: J220.5, U220.6
/Port_Y+/D6: J220.10, U220.11
/Port_Y+/D7: J220.11, U220.10
/Port_Y+/D8: J220.12, U220.9
/Port_Y-/!RESET: R231.1, U230.2
/Port_Y-/A0: R232.2, R234.1, U230.16
/Port_Y-/A1: R233.2, R235.1, U230.15
/Port_Y-/D1: J230.3, U230.4
/Port_Y-/D2: J230.4, U230.5
/Port_Y-/D3: J230.5, U230.6
/Port_Y-/D6: J230.10, U230.11
/Port_Y-/D7: J230.11, U230.10
/Port_Y-/D8: J230.12, U230.9
/SCL: J1.18B, R2.2, U200.1, U210.1, U220.1, U230.1
/SDA: J1.17B, R1.2, U200.3, U210.3, U220.3, U230.3
/SENSOR_X+: C202.1, J1.26B, R200.1, U200.8
/SENSOR_X-: C212.1, J1.24B, R210.1, U210.8
/SENSOR_Y+: C222.1, J1.23B, R220.1, U220.8
/SENSOR_Y-: C232.1, J1.25B, R230.1, U230.8
GND: C1.1, C2.1, C110.2, C111.2, C112.2, C114.2, C115.2, C130.2, C131.2, C132.2, C134.2, C135.2, C150.2, C151.2, C152.2, C154.2, C155.2, C170.2, C171.2, C172.2, C174.2, C175.2, C200.1, C201.2, C202.2, C203.2, C210.1, C211.2, C212.2, C213.2, C220.1, C221.2, C222.2, C223.2, C230.1, C231.2, C232.2, C233.2, D110.A, D130.A, D150.A, D170.A, J1.1B, J1.32A, J1.32B, J2.1, J3.1, J4.1, J5.1, J6.10, J6.13, J6.16, J6.18, J7.2, J7.3, J13.1, J105.2, J105.7, J105.8, J105.13, J105.SHLD, J200.2, J200.7, J200.8, J200.13, J200.SHLD, J202.1, J210.2, J210.7, J210.8, J210.13, J210.SHLD, J212.1, J220.2, J220.7, J220.8, J220.13, J220.SHLD, J222.1, J230.2, J230.7, J230.8, J230.13, J230.SHLD, J234.1, R116.2, R136.2, R156.2, R176.2, R200.2, R204.2, R205.2, R210.2, R214.2, R215.2, R220.2, R224.2, R225.2, R230.2, R234.2, R235.2, U110.2, U130.2, U150.2, U170.2, U200.14, U210.14, U220.14, U230.14
unnamed: C101.1, R100.2, R101.2, U100.1
unnamed: C102.1, R105.2, R106.1, U100.5
unnamed: C103.1, R102.2, U100.7
unnamed: C103.2, R103.2, U100.6
unnamed: C111.1, R110.2, R111.2, U110.1
unnamed: C112.1, R115.2, R116.1, U110.5
unnamed: C113.1, R112.2, U110.7
unnamed: C113.2, R113.2, U110.6
unnamed: C121.1, R120.2, R121.2, U120.1
unnamed: C122.1, R125.2, R126.1, U120.5
unnamed: C123.1, R122.2, U120.7
unnamed: C123.2, R123.2, U120.6
unnamed: C131.1, R130.2, R131.2, U130.1
unnamed: C132.1, R135.2, R136.1, U130.5
unnamed: C133.1, R132.2, U130.7
unnamed: C133.2, R133.2, U130.6
unnamed: C141.1, R140.2, R141.2, U140.1
unnamed: C142.1, R145.2, R146.1, U140.5
unnamed: C143.1, R142.2, U140.7
unnamed: C143.2, R143.2, U140.6
unnamed: C151.1, R150.2, R151.2, U150.1
unnamed: C152.1, R155.2, R156.1, U150.5
unnamed: C153.1, R152.2, U150.7
unnamed: C153.2, R153.2, U150.6
unnamed: C161.1, R160.2, R161.2, U160.1
unnamed: C162.1, R165.2, R166.1, U160.5
unnamed: C163.1, R162.2, U160.7
unnamed: C163.2, R163.2, U160.6
unnamed: C171.1, R170.2, R171.2, U170.1
unnamed: C172.1, R175.2, R176.1, U170.5
unnamed: C173.1, R172.2, U170.7
unnamed: C173.2, R173.2, U170.6
unnamed: J6.11, R4.1
unnamed: J6.12, R3.2
unnamed: R101.1, U100.8
unnamed: R111.1, U110.8
unnamed: R121.1, U120.8
unnamed: R131.1, U130.8
unnamed: R141.1, U140.8
unnamed: R151.1, U150.8
unnamed: R161.1, U160.8
unnamed: R171.1, U170.8
Z+D_A: J105.6, J200.6, J210.6, J220.6, J230.6, U200.7, U210.7, U220.7, U230.7
Z+D_B: J105.9, J200.9, J210.9, J220.9, J230.9, U200.12, U210.12, U220.12, U230.12

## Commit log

2018-02-04 The real first commit
    [panel-connector.kicad_pcb, panel-connector.sch, port.sch]
2018-02-04 Added mux
    [panel-connector.kicad_pcb, panel-connector.sch, port.sch]
2018-02-05 Added MPPT circuit. MPPT circuit copied from EPS board. MPPT on EPS board should be deleted. Should the negative output of the MPPT circuit be connected to ground or segregated?
    [mppt.sch, panel-connector.sch, port.sch]
2018-02-16 Assigned some footprints and connected some nets
    [mppt.sch, panel-connector.kicad_pcb, panel-connector.sch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]
2018-02-18 Begand layout of connectors and added 3d models. The +Z connector will be placed only on the -X side of the board but because of the schematic hierarchy the net shows it is connected to all sides; ig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
    [mppt.sch, panel-connector.kicad_pcb, panel-connector.sch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]
2018-02-18 populated mppt schematic and layed out mppt circuit
    [mppt.sch, panel-connector.kicad_pcb, panel-connector.sch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]
2018-02-22 Added decoupling to connector
    [mppt.sch, panel-connector.kicad_pcb, panel-connector.sch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]
2018-02-25 layed out MPPT
    [mppt.sch, panel-connector.kicad_pcb, panel-connector.sch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]
2018-02-26 generated 3d model with gps
    [mppt.sch, panel-connector.kicad_pcb, panel-connector.sch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]
2018-02-26 added 3d models
    [mppt.sch, panel-connector.kicad_pcb]
2018-03-04 placed mppt circuits
    [mppt.sch, panel-connector.kicad_pcb, panel-connector.sch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]
2018-03-11 routing complete except for GPS_RST
    [mppt.sch, panel-connector.kicad_pcb, panel-connector.sch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]
2018-03-11 routing complete
    [panel-connector.kicad_pcb, panel-connector.sch]
2018-03-19 optimized reference layout
    [mppt.sch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]
2018-03-22 moved DC connection to eps board inorder to avoid RBF switch above on the eps board
    [panel-conn-BOM.csv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]
2018-03-22 generated gerbers
    [mppt.sch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]
2018-03-22 fixed 3v3 trace collision and GPS PTH grounded
    [panel-connector-B.Cu.gbr, panel-connector-B.Mask.gbr, panel-connector-B.Paste.gbr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]
2018-04-21 solder mask fixed to conform to min 150um webbing requirement
2018-04-21 added file that should have been in previous commit
    [panel-connector.kicad_pcb]
